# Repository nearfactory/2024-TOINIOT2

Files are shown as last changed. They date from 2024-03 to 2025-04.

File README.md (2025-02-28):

# TOINIOT2 2024 Main-Repo

TOINIOT² 2024年度 開発用メインリポジトリ

回路/基板データ・CADデータ・プログラムコード・プレゼンシートなどのデータ共有/保存用

[現時点での設計](https://a360.co/4b5pnYN)

[チーム内Wiki](https://github.com/nearfactory/2024-TOINIOT2/wiki)

## Follow us!

* X (Twitter) | [@toiniot2](https://x.com/toiniot2/)

* Instagram | [toiniot2](https://www.instagram.com/toiniot2/)

* YouTube | [@TOINIOT2](https://www.youtube.com/channel/UCjIjmQF-FIEdHT7s-4lD-6A)

* Team Blog | [TOINIOT² Blog](https://toiniot2-wakayama.github.io/Main/index.html)

## Presentation-Sheet

### 関西ブロック大会 2025.01.14 掲出
TOINIOT2-Kansai-NoName

### リツモリカップ 2025.02.23 掲出
TOINIOT2-Ritsumori

## Rules
* 📂 Discord上の _#GitHub_ チャンネルを活用してアップロード済みデータについての情報交換をしっかり!

* 🗣 コミュニケーションを頻繁にとる!!!!

* 👣 目標は高く、活動は地道に。

* 🧪 実験を実験を面倒くさがらない、小さな実験の積み重ねでロボットは完成する。

* 📚 率先して技術・知識の習得につとめる。

* 🤜 自らの担当に縛られすぎず、他の担当の手伝いもできるとベスト。

* 👥 自分が困っているときは遠慮なくメンバーにヘルプを求め、メンバーが困っているときは躊躇せずヘルプする!!!!

* 💪 **これが最後のRCJ。やり残しがないようにしよう。**

## Members
* NearFactory [@nearfactory](https://x.com/nearfactory/)

  機体設計・回路/基板設計・プログラム・プレゼンシート　担当

* maguronoosushi0807 [@_Rts87](https://x.com/_Rts87)

  回路/基板設計・プログラム　担当
  
* 010

  広報・ブログ・機体組立て　担当

* tobi

  電池監視員　担当

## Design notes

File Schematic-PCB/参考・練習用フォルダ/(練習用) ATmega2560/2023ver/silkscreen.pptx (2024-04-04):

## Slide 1

+

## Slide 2

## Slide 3

LineSensor

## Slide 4

BallSensor

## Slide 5

Camera

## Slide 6

DirSensor

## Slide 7

A

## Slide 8

B

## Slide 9

C

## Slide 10

MD1

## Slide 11

MD2

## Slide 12

PWR

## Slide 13

MainBoard

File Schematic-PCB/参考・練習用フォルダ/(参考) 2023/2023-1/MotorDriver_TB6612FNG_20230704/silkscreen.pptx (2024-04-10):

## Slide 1

+

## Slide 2

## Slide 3

M1

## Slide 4

M2

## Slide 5

M3

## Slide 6

M4

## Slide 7

MD

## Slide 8

PWR

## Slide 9

+5V

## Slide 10

+6.6V

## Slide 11

MotorDriver

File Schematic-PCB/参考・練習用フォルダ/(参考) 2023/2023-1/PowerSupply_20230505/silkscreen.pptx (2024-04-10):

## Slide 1

+

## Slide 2

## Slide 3

Power

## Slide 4

VIN

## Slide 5

MD

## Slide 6

Main

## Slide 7

Line

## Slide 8

Kicker

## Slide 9

DCDC
Conv.

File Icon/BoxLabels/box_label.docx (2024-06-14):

SENSOR

CRIMPING

BATTERY & CHARGER

OMNI WHEEL

CABLE

3D-PRINTERED ITEM

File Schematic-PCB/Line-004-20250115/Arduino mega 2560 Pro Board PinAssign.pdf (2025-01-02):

3.0.1 2025.01.01

D32 | Line-01
D34 | Line-02
D38 | Line-03
D37 | Line-04
D36 | Line-05

General Pin Input/Output

D33 | Line-06
D39 | Line-07
D4 | Line-08
D12 | Line-09
D14 | Line-10
D15 | Line-11
D16 | Line-12
D17 | Line-13
D22 | Line-14
D29 | Line-15
D24 | Line-16
D25 | Line-17
D26 | Line-18
D27 | Line-19
D42 | Line-20
D45 | Line-21
D44 | Line-22
D43 | Line-23
D41 | Line-24
D48 | Line-25
D47 | Line-26
D46 | Line-Front
D5 | Line-Left
D23 | Line-Back
D40 | Line-Right
D13 | LED_BUILTIN
A0 | Line-Left [Raw]
A1 | Line-09 [Raw]
A2 | Line-05 [Raw]
A3 | Line-11 [Raw]
A4 | Line-03 [Raw]
A5 | Line-13 [Raw]
A6 | Line-01 [Raw]
A7 | Line-Back [Raw]
A8 | Line-Front [Raw]
A9 | Line-15 [Raw]
A10 | Line-23 [Raw]
A11 | Line-17 [Raw]
A12 | Line-21 [Raw]
A13 | Line-19 [Raw]
A14 | Line-Right [Raw]
A15 | Line-07 [Raw]

Analog Sensing

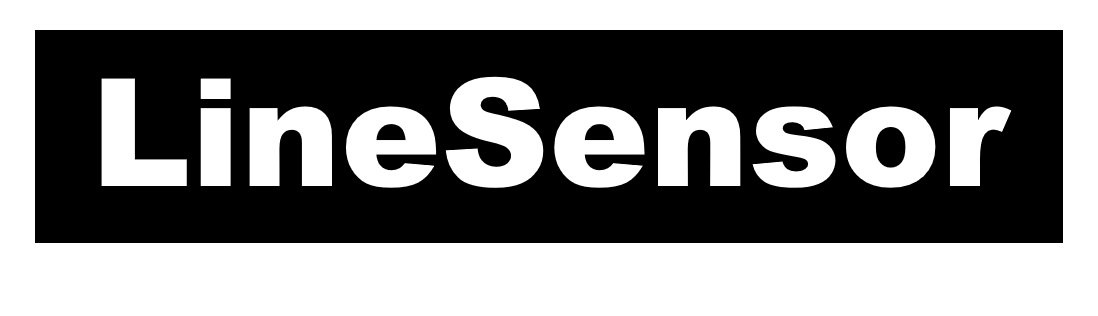
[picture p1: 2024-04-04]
Schematic-PCB/参考・練習用フォルダ/(練習用) ATmega2560/2023ver/LineSensor.png

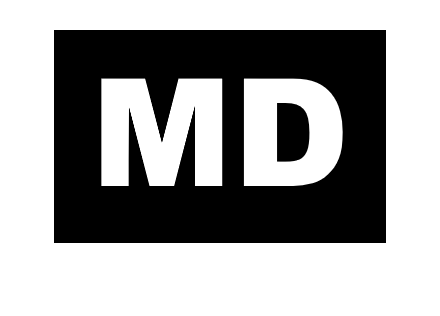
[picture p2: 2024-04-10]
Schematic-PCB/参考・練習用フォルダ/(参考) 2023/2023-1/PowerSupply_20230505/MD.png

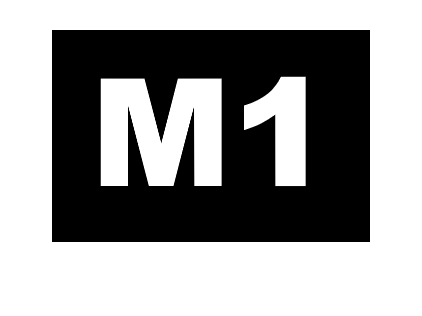
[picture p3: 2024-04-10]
Schematic-PCB/参考・練習用フォルダ/(参考) 2023/2023-1/MotorDriver_TB6612FNG_20230704/M1.png

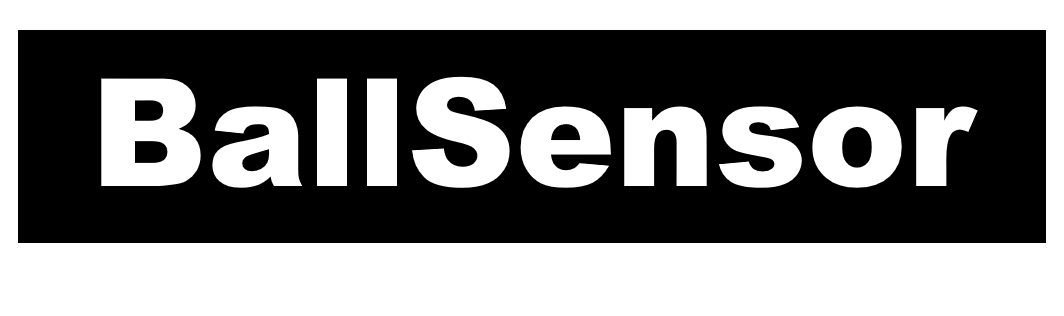
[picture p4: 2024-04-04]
Schematic-PCB/参考・練習用フォルダ/(参考) 2023/2023-1/MainBoard_ATMega2560Pro_20230629/BallSensor.png

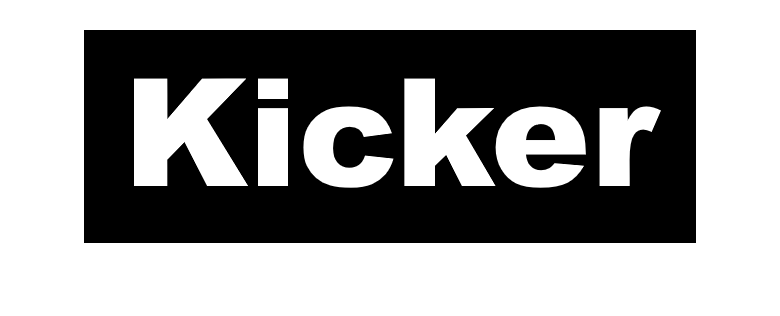
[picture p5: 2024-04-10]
Schematic-PCB/参考・練習用フォルダ/(参考) 2023/2023-1/PowerSupply_20230505/Kicker.png

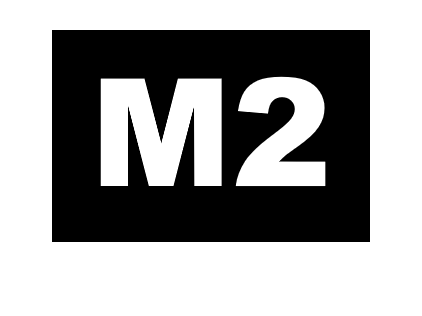
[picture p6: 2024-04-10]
Schematic-PCB/参考・練習用フォルダ/(参考) 2023/2023-1/MotorDriver_TB6612FNG_20230704/M2.png

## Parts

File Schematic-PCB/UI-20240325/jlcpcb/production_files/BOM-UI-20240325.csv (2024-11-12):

Comment | Designator | Footprint | LCSC
0.1uF | C1,C2,C3,C4 | C_0603_1608Metric | C14663
1K | R1,R3,R5,R7,R9 | R_0603_1608Metric | C21190
330 | R10 | R_0603_1608Metric | C23138
10K | R11,R2,R4,R6,R8 | R_0603_1608Metric | C25804

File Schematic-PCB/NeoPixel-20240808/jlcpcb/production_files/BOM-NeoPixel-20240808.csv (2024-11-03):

Comment | Designator | Footprint | LCSC | Quantity
0.1uF | C1,C10,C11,C12,C13,C14,C15,C16,C2,C3,C4,C5,C6,C7,C8,C9 | C_0603_1608Metric | C14663 | 16
WS2812B | D1,D10,D11,D12,D13,D14,D15,D16,D2,D3,D4,D5,D6,D7,D8,D9 | WS2812B 5.0x5.0mm | C2843785 | 16

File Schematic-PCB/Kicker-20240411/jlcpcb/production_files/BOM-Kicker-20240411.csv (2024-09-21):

Comment | Designator | Footprint | LCSC
0.33u | C2,C3 | C_0603_1608Metric | C107058
TSSP58P38 | U1,U2 | Vishay_MINICAST-3Pin | C144844
0.1uF | C5,C7 | C_0603_1608Metric | C14663
330 | R3 | R_0603_1608Metric | C23138
39K | R1,R2 | R_0603_1608Metric | C23153
10K | R4,R5 | R_0603_1608Metric | C25804

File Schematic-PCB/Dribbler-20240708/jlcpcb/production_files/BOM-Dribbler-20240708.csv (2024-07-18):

Comment | Designator | Footprint | LCSC
330 | R1,R2 | R_0603_1608Metric | C23138

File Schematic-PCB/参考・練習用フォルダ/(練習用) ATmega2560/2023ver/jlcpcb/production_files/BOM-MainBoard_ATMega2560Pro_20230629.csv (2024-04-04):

Comment | Designator | Footprint | LCSC
10K | R10,R12,R6,R8 | R_0805_2012Metric | C17414
1K | R11,R13,R5,R7,R9 | R_0805_2012Metric | C17513
330 | R1,R2,R3,R4 | R_0805_2012Metric | C17630
C | C1 | C_0805_2012Metric | C45783

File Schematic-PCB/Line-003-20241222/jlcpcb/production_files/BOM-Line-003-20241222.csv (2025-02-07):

Comment | Designator | Footprint | LCSC | Quantity
100nF | C1,C10,C11,C12,C13,C14,C15,C16,C17,C18,C19,C2,C3,C4,C5,C6,C7,C8,C9 | C_0603_1608Metric | C14663 | 19
10uF | C21,C22 | C_0805_2012Metric | C15850 | 2
1K | R81,R84 | R_0603_1608Metric | C21190 | 2
100 | R86,R87 | R_0603_1608Metric | C22775 | 2
330 | R79,R88 | R_0603_1608Metric | C23138 | 2
Line-PDWN2 | R27,R28,R29,R30 | R_0603_1608Metric | C25804 | 4
RESET | SW1 | Tactile1 | C2844407 | 1
Line-PDWN | R1,R10,R11,R12,R13,R14,R15,R16,R17,R18,R19,R2,R20,R21,R22,R23,R24,R25,R26,R3,R4,R5,R6,R7,R8,R9 | R_0603_1608Metric | C4184 | 26
75 | R31,R32,R33,R34,R35,R36,R37,R38,R39,R40,R41,R42,R43,R44,R45,R46,R47,R48,R49,R50,R51,R52,R53,R54,R55,R56,R57,R58,R59,R60,R61,R62,R63,R64,R65,R66,R67,R68,R69,R70,R71,R72,R73,R74,R75,R76 | R_0603_1608Metric | C4275 | 46
LM393 | U47,U48,U49,U50,U51,U52,U53,U54,U55,U56,U57,U58,U59,U60,U61 | SOP-8_3.9x4.9mm_P1.27mm | C7955 | 15

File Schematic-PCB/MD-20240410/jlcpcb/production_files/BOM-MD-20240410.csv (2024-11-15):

Comment | Designator | Footprint | LCSC | Quantity
0.1u | C7,C8 | C_0603_1608Metric | C14663 | 2
~ | U1,U2,U3,U4 | HTSSOP-16-1EP_4.4x5mm_P0.65mm_EP3.4x5mm | C1855818 | 4
4.7u | C3,C4 | C_0603_1608Metric | C19666 | 2
220n | C10,C12,C14,C2 | C_0603_1608Metric | C21120 | 4
22n | C1,C11,C13,C9 | C_0603_1608Metric | C21122 | 4
2.49k | R12,R16,R4,R8 | R_0603_1608Metric | C22908 | 4
330 | R1 | R_0603_1608Metric | C23138 | 1
10k | R13,R17,R20,R21,R22,R23,R3,R9 | R_0603_1608Metric | C25804 | 8
Conn_main | J8 | TE_1-84953-5_1x15-1MP_P1.0mm_Horizontal | C2914102 | 1
20k | R11,R15,R19,R7 | R_0603_1608Metric | C4184 | 4

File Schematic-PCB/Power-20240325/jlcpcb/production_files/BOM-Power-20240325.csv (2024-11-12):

Comment | Designator | Footprint | LCSC
1K | R4 | R_0603_1608Metric | C21190
1.2K | R3,R7 | R_0603_1608Metric | C22765
1.5K | R1 | R_0603_1608Metric | C22843
10 | R5 | R_0603_1608Metric | C22859
330 | R6 | R_0603_1608Metric | C23138
680 | R2 | R_0603_1608Metric | C23228
22uF | C1,C3 | C_0603_1608Metric | C45783
10uF | C2,C6 | C_0603_1608Metric | C96446
Conn_01x02_Pin | J6 | JST_XH_S2B-XH-A-1_1x02_P2.50mm_Horizontal

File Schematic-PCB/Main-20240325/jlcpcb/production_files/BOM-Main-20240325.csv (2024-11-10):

Comment | Designator | Footprint | LCSC | Quantity
TSSP4038 | U10,U11,U12,U13,U14,U15,U16,U17,U18,U3,U4,U5,U6,U7,U8,U9 | TSSP4038 | C143753 | 16
0.1uF | C10,C11,C12,C3,C4,C5,C6,C7,C8,C9 | C_0603_1608Metric | C14663 | 10
1K | R3,R4 | R_0603_1608Metric | C21190 | 2
330 | R5,R7 | R_0603_1608Metric | C23138 | 2
39K | R10,R11,R12,R13,R14,R15,R18,R19,R20,R21,R22,R23,R24,R25,R8,R9 | R_0603_1608Metric | C23153 | 16
10K | R16,R17,R6 | R_0603_1608Metric | C25804 | 3
0.33uF | C13,C14,C15,C16,C17,C18,C19,C20,C21,C22,C23,C24,C25,C26,C27,C28 | C_0603_1608Metric | C282682 | 16
Conn_MD | J5 | 1.0K-FX-15PWB | C2914102 | 1

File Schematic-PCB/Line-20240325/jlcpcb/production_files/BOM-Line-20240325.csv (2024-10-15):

Comment | Designator | Footprint | LCSC
0.1uF | C2,C3,C4 | C_0603_1608Metric | C14663
1K | R97 | R_0603_1608Metric | C21190
Line-Pulldown | R47,R48,R49,R50,R51,R52,R53,R54,R55,R56,R57,R58,R59,R60,R61,R62,R63,R64,R65,R66,R67,R68,R69,R70,R71,R72,R73,R74,R75,R76,R77,R78,R79,R80,R81,R82,R83,R84,R85,R86,R87,R88,R89,R90,R91,R92 | R_0603_1608Metric | C22809
330 | R93,R94,R95,R96 | R_0603_1608Metric | C23138
75 | R1,R10,R11,R12,R13,R14,R15,R16,R17,R18,R19,R2,R20,R21,R22,R23,R24,R25,R26,R27,R28,R29,R3,R30,R31,R32,R33,R34,R35,R36,R37,R38,R39,R4,R40,R41,R42,R43,R44,R45,R46,R5,R6,R7,R8,R9 | R_0603_1608Metric | C4275
10uF | C5 | C_0603_1608Metric | C96446

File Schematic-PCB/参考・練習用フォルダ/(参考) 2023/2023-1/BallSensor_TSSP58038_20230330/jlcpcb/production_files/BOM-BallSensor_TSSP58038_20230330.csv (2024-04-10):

Comment | Designator | Footprint | LCSC
TSSP58038 | U1,U10,U11,U12,U13,U14,U15,U16,U2,U3,U4,U5,U6,U7,U8,U9 | TSSP58038 | C144844
C | C18,C19,C20,C21,C22,C23,C24,C25 | C_0603_1608Metric | C14663
C | C10,C11,C12,C13,C14,C15,C16,C17,C2,C3,C4,C5,C6,C7,C8,C9 | C_0603_1608Metric | C1615
~ | D10,D11,D12,D13,D14,D15,D16,D17,D2,D3,D4,D5,D6,D7,D8,D9 | WS2812B | C2761795
R | R1,R10,R11,R12,R13,R14,R15,R16,R17,R2,R3,R4,R5,R6,R7,R8,R9 | R_0603_1608Metric | C4275
Conn_01x20_Male | J1 | IDC-Header_2x10_P2.54mm_Vertical

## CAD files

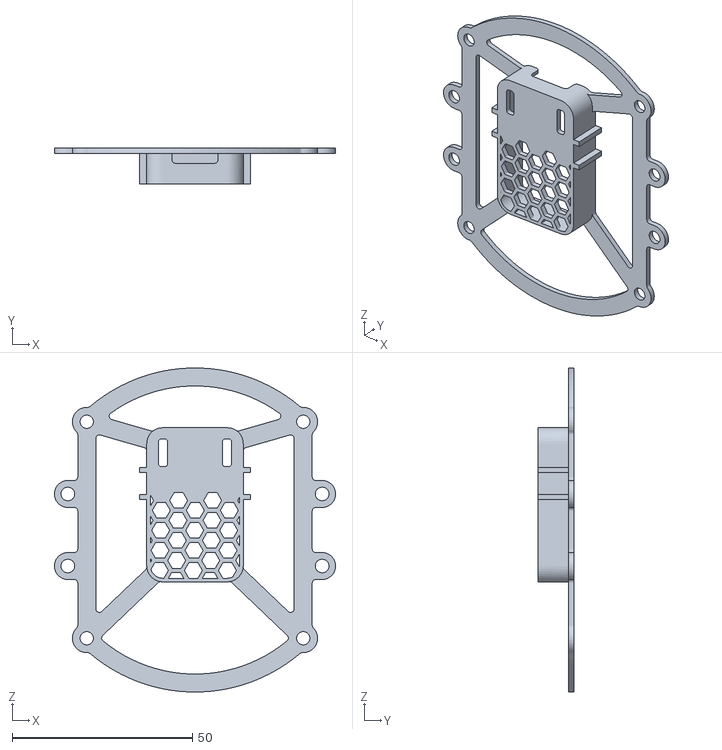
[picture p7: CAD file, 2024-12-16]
Design/3D [自家製]/camera-supporter/[iot2][006][camera-supporter][main].stl
78.1 x 10.0 x 90.0

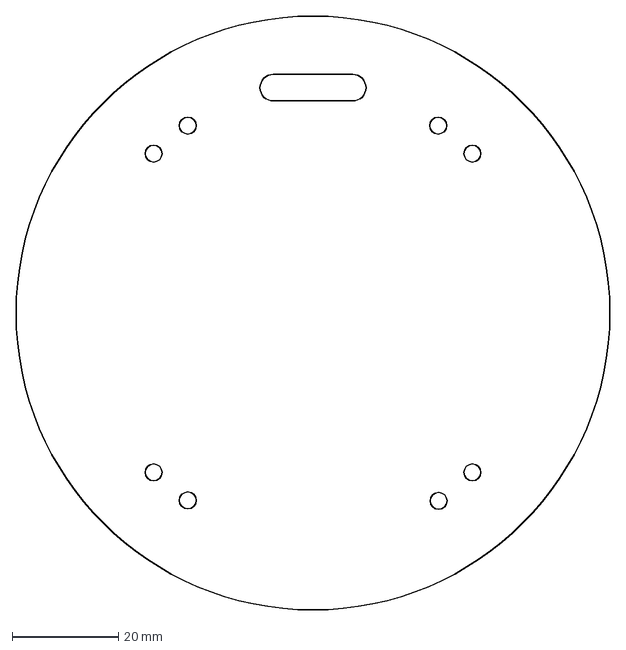
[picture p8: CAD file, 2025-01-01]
Schematic-PCB/Main-003-20241229/outline/[iot2][003][main-003-outline].dxf
112.0 x 112.0 mm

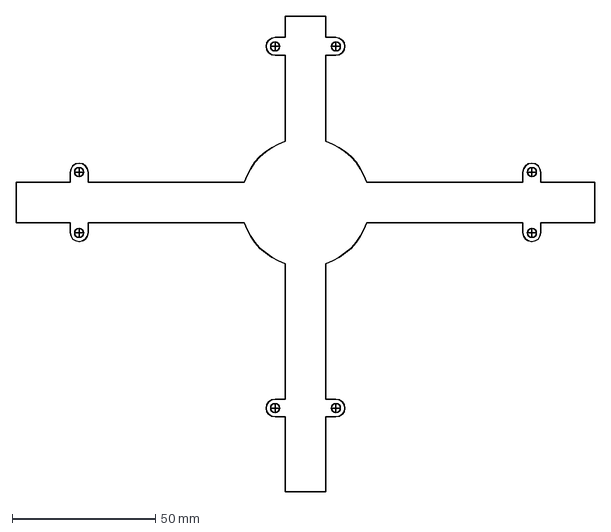
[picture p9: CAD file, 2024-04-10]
Schematic-PCB/参考・練習用フォルダ/(参考) 2023/2023-1/LineSensor_20230418/main.dxf
202.0 x 166.0 mm

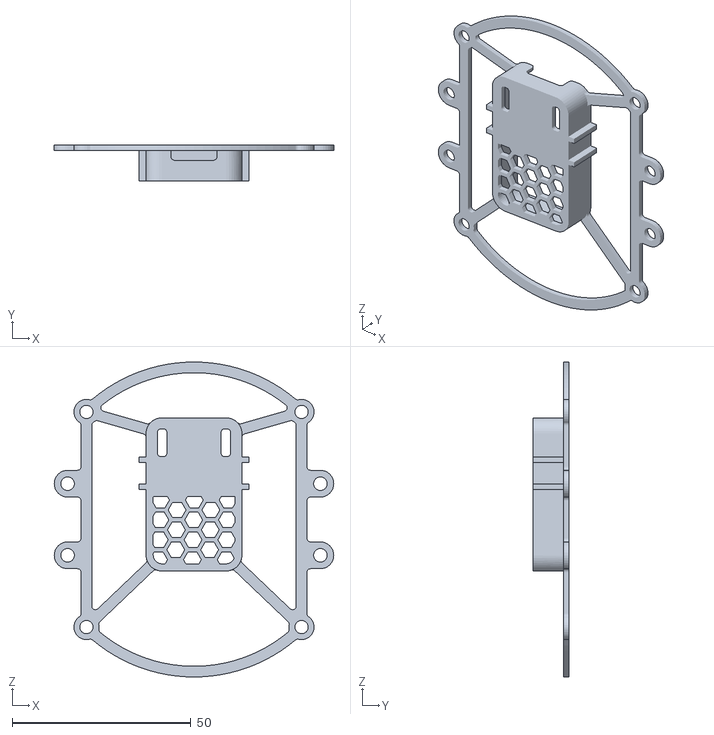
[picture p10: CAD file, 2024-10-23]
Design/3D [自家製]/camera-supporter/[iot2][005][camera-supporter][main].stl
78.1 x 10.0 x 88.0

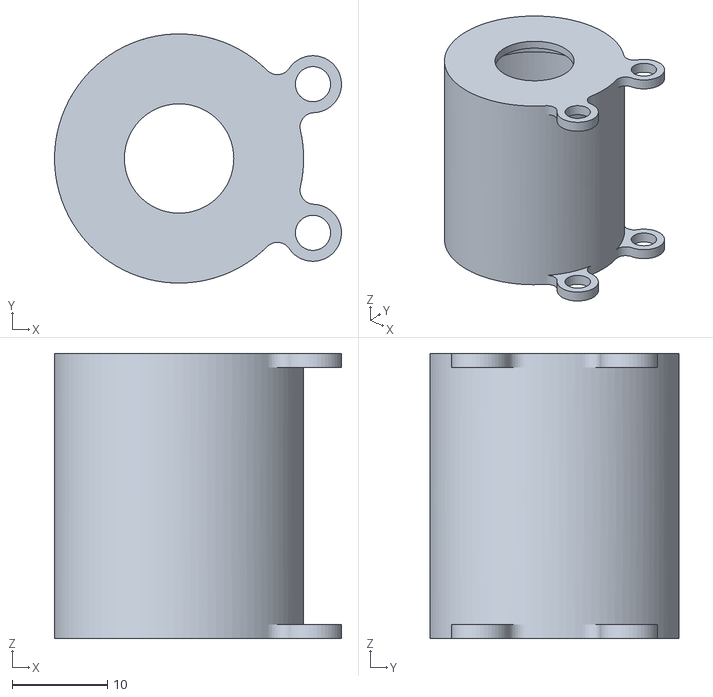
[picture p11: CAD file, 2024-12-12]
Design/3D [自家製]/dribbler/dribbler-004/[iot2][003][dribbler-004][main].stl
30.2 x 26.2 x 30.0

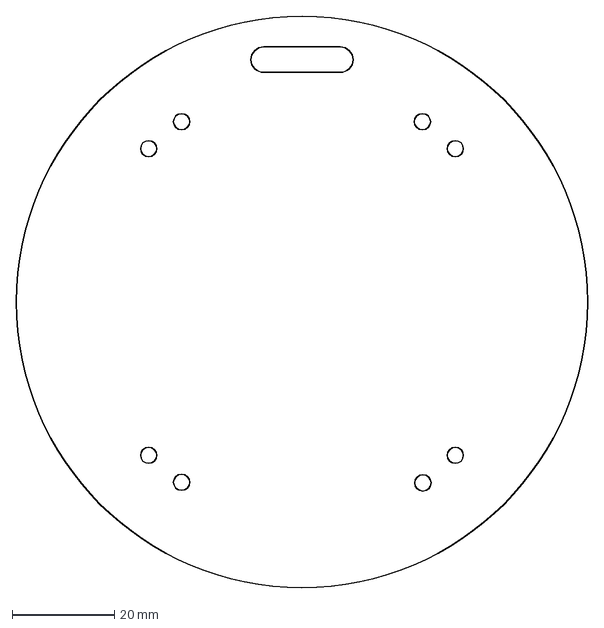
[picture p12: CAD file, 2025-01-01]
Schematic-PCB/Main-003-20241229/outline/[iot2][002][main-003-outline].dxf
112.0 x 112.0 mm

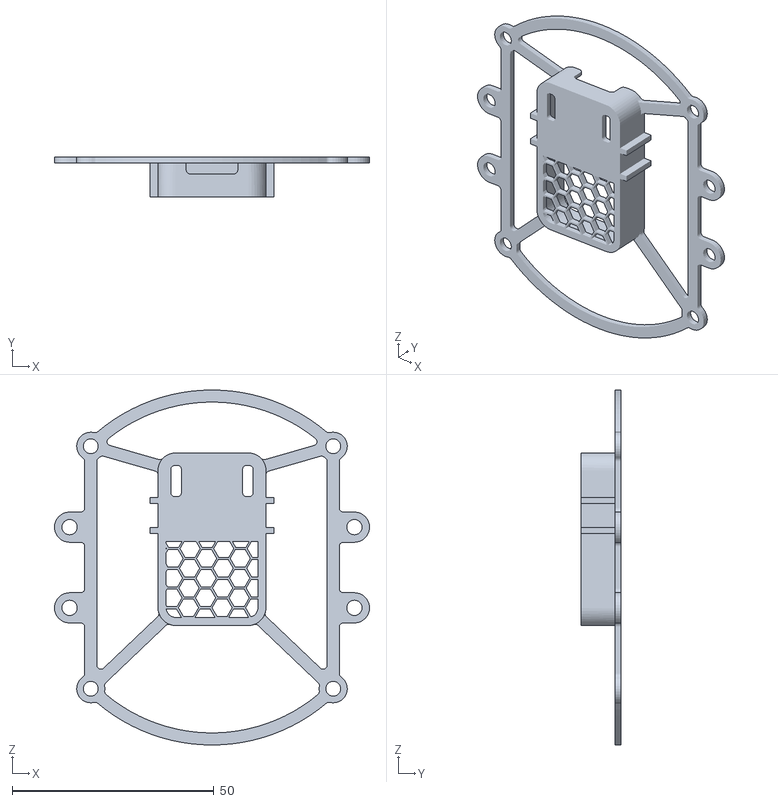
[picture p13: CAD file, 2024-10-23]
Design/3D [自家製]/camera-supporter/[iot2][004][camera-supporter][main].stl
78.1 x 10.0 x 88.0

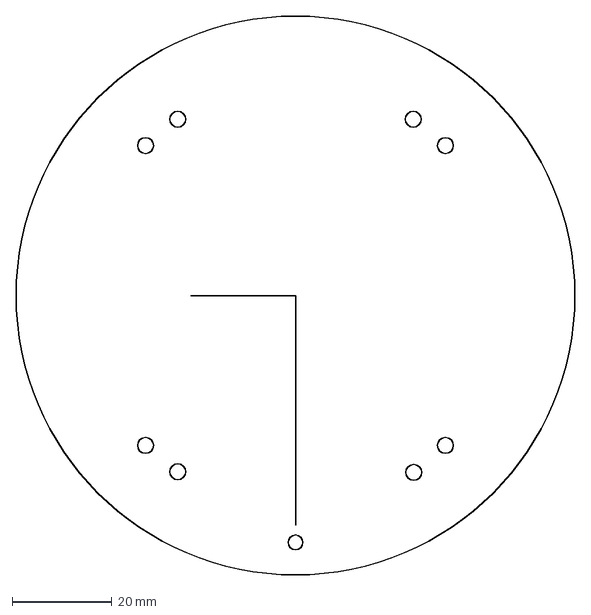
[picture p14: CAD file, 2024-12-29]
Schematic-PCB/Main-003-20241229/outline/[iot2][001][main-003-outline].dxf
112.0 x 112.0 mm

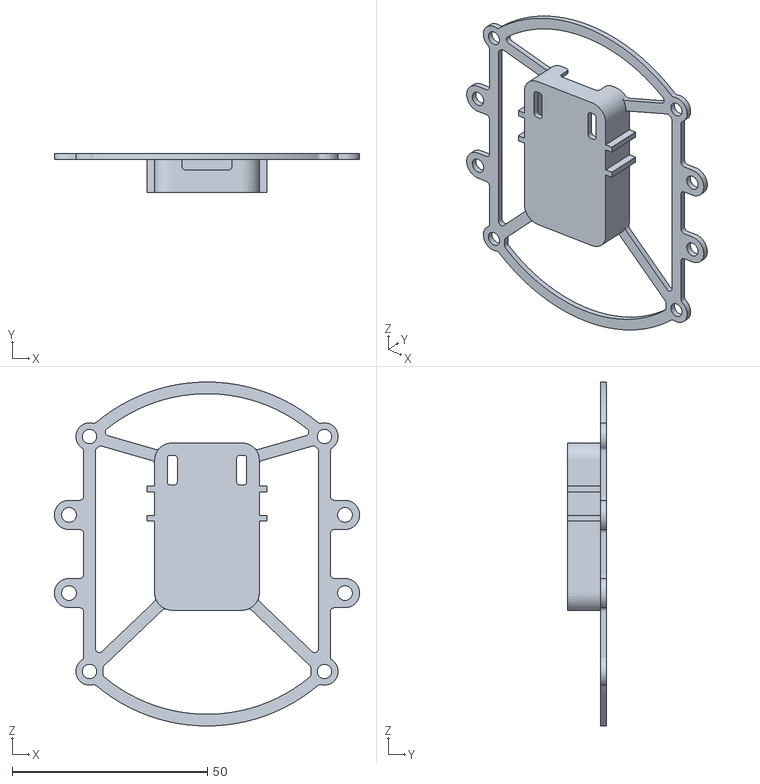
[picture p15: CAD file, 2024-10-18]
Design/3D [自家製]/camera-supporter/[iot2][003][camera-supporter][main].stl
78.1 x 10.0 x 88.0

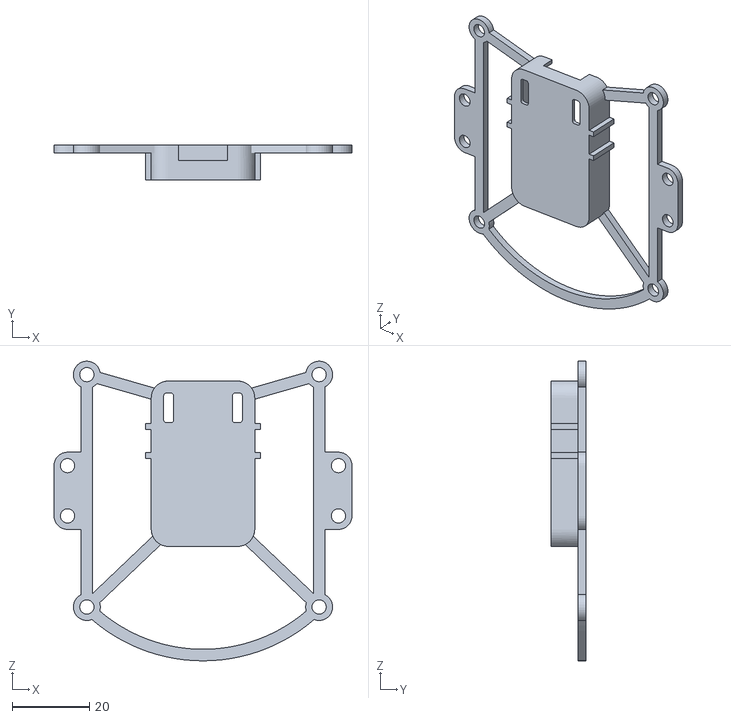
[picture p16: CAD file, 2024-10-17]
Design/3D [自家製]/camera-supporter/[iot2][002][camera-supporter][main].stl
77.1 x 9.00 x 77.5

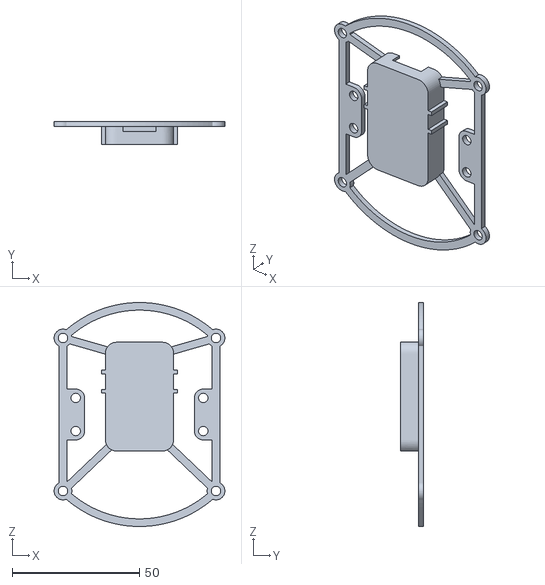
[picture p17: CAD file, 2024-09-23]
Design/3D [自家製]/camera-supporter/[iot2][001][camera-supporter][main].stl
67.1 x 9.00 x 88.0

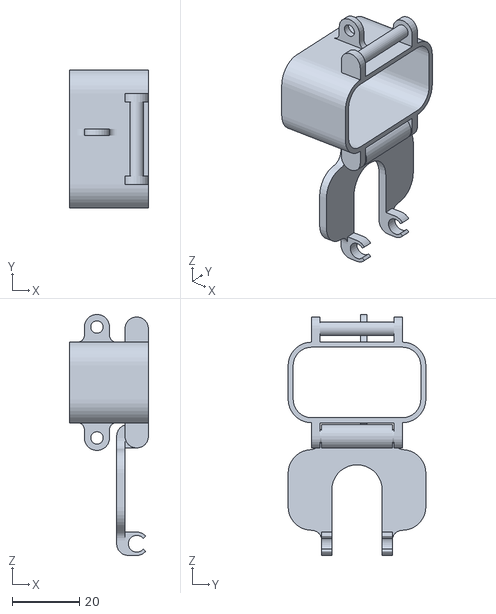
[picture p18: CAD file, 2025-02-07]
Design/3D [1000万]/[iot2][battery-R-lid][001].stl
23.5 x 41.0 x 71.7

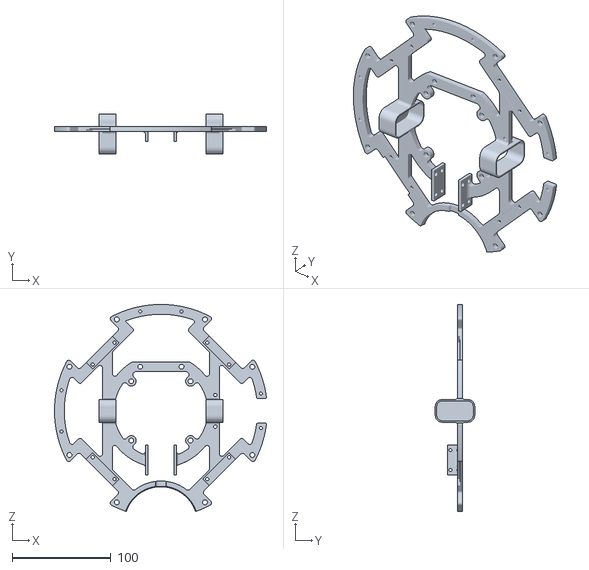
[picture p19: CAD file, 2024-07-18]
Design/3D [外注決定]/002-01/002-Top-004.stl
215.1 x 40.2 x 210.1

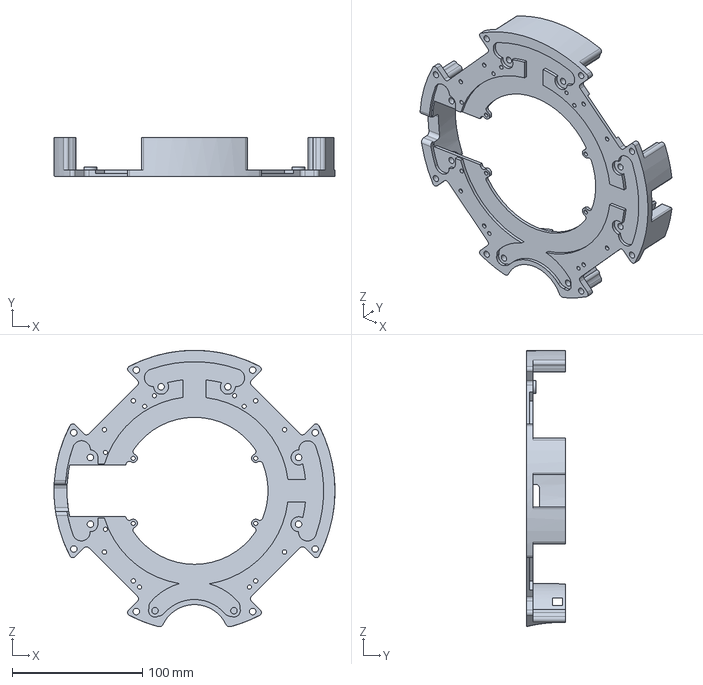
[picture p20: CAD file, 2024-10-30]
Design/3D [外注決定]/002-02/002-bottom-02.step
216.0 x 30.0 x 212.4 mm

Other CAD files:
Design/3D [外注決定]/003-01/iot2 003 top 3.stl
Design/3D [自家製]/actuator-cover/motorcover#002[iot2].stl
Design/3D [自家製]/ball-cover-for-main003/[iot2][ball-cover-m3][002].stl
Design/3D [自家製]/battery/[iot2][003][battery-2-2].stl
Design/3D [外注決定]/002-01/002-Bottom-002.stl
Design/3D [外注決定]/002-01/002-Bottom-004.stl
Design/3D [外注決定]/002-01/002-Bottom.stl
Design/3D [外注決定]/002-01/002-Top-002.stl
Design/3D [外注決定]/002-01/002-Top-003.stl
Design/3D [外注決定]/002-01/002-Top.stl
Design/3D [外注決定]/002-02/002-top-02.step
Design/3D [外注決定]/002-02/[iot2][002][bottom][2].stl
Design/3D [外注決定]/002-02/[iot2][002][top][2].stl
Design/3D [外注決定]/003-01/iot2 003 bottom 1.stl
Design/3D [外注決定]/003-01/iot2 003 bottom 2.stl
Design/3D [外注決定]/003-01/iot2 003 top 1.stl
Design/3D [外注決定]/003-01/iot2 003 top 2.stl
Design/3D [自家製]/actuator-cover/motorcover#001[iot2].stl
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

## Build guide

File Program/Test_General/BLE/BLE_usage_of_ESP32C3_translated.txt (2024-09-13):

こんにちは。
ここで、BLE を使用して 2 つの ESP32C3 を接続する方法の例を確認できます。
https://wiki.seeedstudio.com/
XIAO_ESP32C3_Bluetooth_使用法/
よろしく！
EICO
テクニカルサポートチームを参照

こんにちは。
私はサイエンスクラブに所属する日本人学生です。
私は部活動として、人間が制御せずにサッカーをするロボットを作っています。
無線通信を行うために、ESP32C3モジュールを使用する予定です。
しかし、2台のESP32C3を無線で接続する方法が見つからなかったので、それが可能かどうかを確認したいと思います。
ESP32C3を2つ接続する方法を教えていただければ幸いです。
ありがとう。

ご回答ありがとうございます。
ある ESP32C3 を別の ESP32C3 に Bluetooth 経由で接続できるかどうかを確認したいと思います。
回答のリンクには、2 台の ESP32C3 を Bluetooth 経由で接続する例はなく、1 台の ESP32C3 を Bluetooth 経由でスマートフォンまたは PC に接続するだけです。
2台のESP32C3を接続する方法を教えていただけますか?
ありがとう：）

こんにちは。
なるほど、S3 の例を参照してください。C3 でも機能するはずです。
https://wiki.seeedstudio.com/
xiao_esp32s3_bluetooth/
よろしく！

ESP32C3を別のESP32C3に接続できるか確認したい
Bluetooth経由のESP32C3。
あなたの応答のリンクには、2 つの ESP32C3 を接続する例がありません。
Bluetooth 経由ですが、1 つの ESP32C3 をスマートフォンまたは PC に接続するだけです。
ブルートゥース。
2台のESP32C3を接続する方法を教えていただけますか?
ありがとう：）

こんにちは。
ここで、BLE を使用して 2 つの ESP32C3 を接続する方法の例を確認できます。
https://wiki.seeedstudio.com/
XIAO_ESP32C3_Bluetooth_使用法/
よろしく！

こんにちは。
ご返答ありがとうございます。
ESP32S3の技術資料を参考にさせていただきます。
ご協力ありがとうございました！

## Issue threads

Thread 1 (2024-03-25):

モーター選定

Toiniot2-Wakayama, 2024-03-25:
- Pololu
- Maxon
- 秋月モーター
- 中華コアレス
- その他

選定時は回転数 (RPM) とトルク (mNm、kg*cmなど）に着目の上で選定する

nearfactory, 2024-03-28:
当初予定していたmaxonモーターと異なるモーターを選定したい

4.5W・13100rpm・29.9 mNm
1-4コ：23,800
5-19コ：21,000

nearfactory, 2024-03-28:
新モーター
https://www.maxongroup.co.jp/maxon/view/product/motor/dcmotor/re/re16/118714
https://www.maxongroup.co.jp/maxon/view/product/motor/dcmotor/re/re16/118715

2つの違い：定格電圧が9Vか12Vか

nearfactory, 2024-04-13:
一旦pololuもmaxonでも対応できるモーターブラケットの設計を完了済み
→maxonが入手できるまではpololu 25D 9.7:1で行く、手に入り次第maxonでやってみる

Closed 2024-06-14.

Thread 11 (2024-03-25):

電源基板回路設計

Toiniot2-Wakayama, 2024-03-25:

nearfactory, 2024-03-28:
電圧監視回路、ヒューズ、電圧計、DCDCコンバーターを搭載予定

DCDCコンバーターについては、従来のOKL-T/6-W12Cを使用するか、新しいDCDCコンバーターを探すか
→ 効率、安全性、価格、性能等を鑑みて検討するべし

nearfactory, 2024-03-29:
DCDCコンバーターは従来のモノを使う予定
→電源基板自体を物理的に保護するようなカバーが欲しいところではある
（偶発的な接触、ショートからの保護等の問題解決、ナット等が落ちて入りこむことを防ぐ目的）

Closed 2024-06-14.

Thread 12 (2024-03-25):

電池選定

Toiniot2-Wakayama, 2024-03-25:
- Li-Fe 2セル
- Li-Fe 3セル
- Ni-MH 8.4V
- Ni-MH 9.6V
- その他充電池

電池容量、電圧、安全性、価格等に着目の上選定する

nearfactory, 2024-03-29:
現状では
・Li-Fe 3セル 9.9V 1450mAh
が有力候補ではある
ただいつもの
・Ni-MH 9.6V 1600mAh
も決して悪くはない、サイズ感的にちょっとあれやけど

nearfactory, 2024-03-29:
**Li-Fe3セル 9.9V 1450mAh**
https://kondo-robot.com/product/life_f3_1450
**↑専用充電器**
https://kondo-robot.com/product/bx-20lf

nearfactory, 2024-03-29:
**Ni-MH 9.6V 1600mAh**
https://www.amazon.co.jp/Melasta-%E3%83%8B%E3%83%83%E3%82%B1%E3%83%AB%E6%B0%B4%E7%B4%A0%E3%83%90%E3%83%83%E3%83%86%E3%83%AA%E3%83%BC-%E3%83%9F%E3%83%8B%E3%82%B3%E3%8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
**↑専用充電器**
https://www.amazon.co.jp/Melasta-%E3%83%8B%E3%83%83%E3%82%B1%E3%83%AB%E6%B0%B4%E7%B4%A0%E3%83%90%E3%83%83%E3%83%86%E3%83%AA%E3%83%BC%E5%85%85%E9%9B%BB%E5%99%A8-%E6%A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

nearfactory, 2024-04-13:
設計はLi-Fe 3セル 9.9V 1450mAhで行っている
Ni-MHへの対応も考えてもいいが、キッカーの搭載が厳しくなる恐れがある（縦にして入れれば何とかなるが...）

Closed 2024-06-14.

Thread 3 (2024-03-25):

カメラ選定

Toiniot2-Wakayama, 2024-03-25:
- 処理速度
- 画素数
- 画質
- プログラミング言語
- サイズ
- 焦点距離

等に着目の上選定する

nearfactory, 2024-03-28:
今のところ
UnitVかPixy2.1を使用予定

UnitV
低価格・低処理速度・普通解像度・Micropython・UART/SPIでの通信

Pixy
高価格・普通処理速度・普通解像度・プログラムなし・I2C/UART/SPIでの通信

使い慣れたPixyで行くか、UnitVという新しい道を切り開くか。

maguronoosushi0807, 2024-03-29:
処理速度の問題を解決できるなら安価なUnitVを使用してみるのでいいと思います。

軽く調べた感じ、デフォルトの重いファームウェアから必要な部分だけを抽出して軽量化しているようです。
https://blog.shirokuma89.dev/20240328/ 「カメラ」の段落より

Closed 2024-06-14.

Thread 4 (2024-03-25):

マイコン選定

Toiniot2-Wakayama, 2024-03-25:
**マイコンは2つ以上使用予定のため、それぞれに適応したマイコンを選定すること**

- メイン処理用
- ボールセンサ用
- ラインセンサ用
- （距離センサ用）
- （MD用）
- （UI用）

等があるため、それぞれに合ったマイコンを選定すること（チップのモノがあるかJLCPCBにどうかも要チェック）

nearfactory, 2024-03-28:
teensy4.1
高処理速度・高価格・SMD化ほぼ不可能・普通サイズ・普通ピン数

STM32
高処理速度・価格？・SMD対応・SMDの場合小サイズ・普通ピン数

STM32については機体に搭載する場合はSMD化が必須→ボードが特大サイズのため

nearfactory, 2024-03-29:
Teesy4.1を使う場合、拡張基板を自作したうえで使用する必要がある
→開発基板に表面実装でしか使えないピンがある
→それを使えるようにするために拡張基板を作る必要がある

nearfactory, 2024-03-29:
teensy4.1は動作電圧が3.3V、
STM32も動作電圧は3.6Vぐらい

nearfactory, 2024-04-13:
メインマイコンにはteensy4.1、サブマイコン（無線・UIなど）でESP32C3（seeed）を使用
ラインセンサ専用マイコンでATmega2560（チップ）を使用予定
→ATmega2560の回路については山本さんor他の誰かしらに必ずDRを求めること（特に書き込み用シリアル変換周り）

Closed 2024-06-14.

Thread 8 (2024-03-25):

ボールセンサ基板回路設計

Toiniot2-Wakayama, 2024-03-25:

nearfactory, 2024-03-29:
使用するセンサ素子で悩み中

TSSP58038かTSSP4038で悩んでる
TSSP58038→2023で使ったやつ、特性もある程度把握できている
TSSP4038→2023でedgeが使ってた、距離と角度に応じたセンサ値の変動が58038よりもきれい、ただ使ったことがない

nearfactory, 2024-03-29:
**TSSP58038**
https://www.mouser.jp/ProductDetail/Vishay-Semiconductors/TSSP58038?qs=lgjwDzixuo29LR1eAo9EoA%3D%3D

**TSSP4038**
https://www.mouser.jp/ProductDetail/Vishay-Semiconductors/TSSP4038?qs=lgjwDzixuo3Ja5hn%252BEmOdw%3D%3D

nearfactory, 2024-03-29:
ちなみにセンサ素子自体の形も微妙に違う
58038は受光部が1/4球+半円柱なのに対して、4038は完全に受光部が半球になってる
多分そのせいで受光時の感度が違う

nearfactory, 2024-03-31:
両方買ってみてセンサ素子による値の違いを見てみるのもあり
→プレゼンシートにかけるのでは？（実験・データ）

Closed 2024-06-14.

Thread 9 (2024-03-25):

ラインセンサ基板回路設計

Toiniot2-Wakayama, 2024-03-25:

nearfactory, 2024-03-30:
使用するLEDの選定について
コート色である緑の補色の**赤色**LEDを使用したい
半値角は30度のモノがいいのでは
→光漏れが少なくなる→ラインセンサカバーの制作が不要になるのでは

今のところの選定
・無極性3mm赤色LED 625nm OSRRH23133A（https://akizukidenshi.com/catalog/g/g111347/）
・3mm赤色LED 624nm 30度 OS5RKA3131A（https://akizukidenshi.com/catalog/g/g104767/）
・低消費3mm 赤色 LED 625nm 1mA OSR5PA3133A-1MA（https://akizukidenshi.com/catalog/g/g116908/）
のうちのどれか

nearfactory, 2024-03-30:
センサ素子自体は、現状のままだとTHTのいつものNJL7502Lを使う予定
（ https://akizukidenshi.com/catalog/g/g102325/ ）

nearfactory, 2024-03-31:
**LED選定について**
個人的には半値角の違いでどのように見えかたが変わるのかを実験してみるのも全然あり

→プレゼンシートにもかけるかも（実験とデータを示そう）

nearfactory, 2024-04-02:
**LEDの選定について**
半減角の認識が違ったので、選定やり直しです。
2023に使っていたものは半減角が60度だったので、それと同じようなものを赤色LEDで調べていたところ、70度のものが見つかりました。
再度LEDの半減角を調べた上で検討していきたいと思います。

・3mm赤色LED 625nm 70度 OSR5JA3Z74A
https://akizukidenshi.com/catalog/g/g111333/

nearfactory, 2024-04-06:
ラインセンサ専用マイコンを積む予定ですが、今のところはATmega2560を積む予定です。
アナログピンが16本あるので、それを使って自動閾値調整をやりたいです。
今考えているのは、閾値設定モードを予め用意しておき、予めいくつかのセンサをアナログピンにも並列で繋いでおき（基本的にすべてのセンサはデジタルで読む予定）そのアナログ値から閾値を自動で算出。その後、FET（MOSFET）に繋いだピン（PWM）でセンサの電源電圧を変更する、という流れです。

nearfactory, 2024-04-13:
コンパレータ
秋月での購入 or JLCPCBでのAssembly
両方ともめどは立っているが...
回路関連はedgeのブログを参考にしつつ山本さんにDR依頼してもいいかも

Closed 2024-06-14.

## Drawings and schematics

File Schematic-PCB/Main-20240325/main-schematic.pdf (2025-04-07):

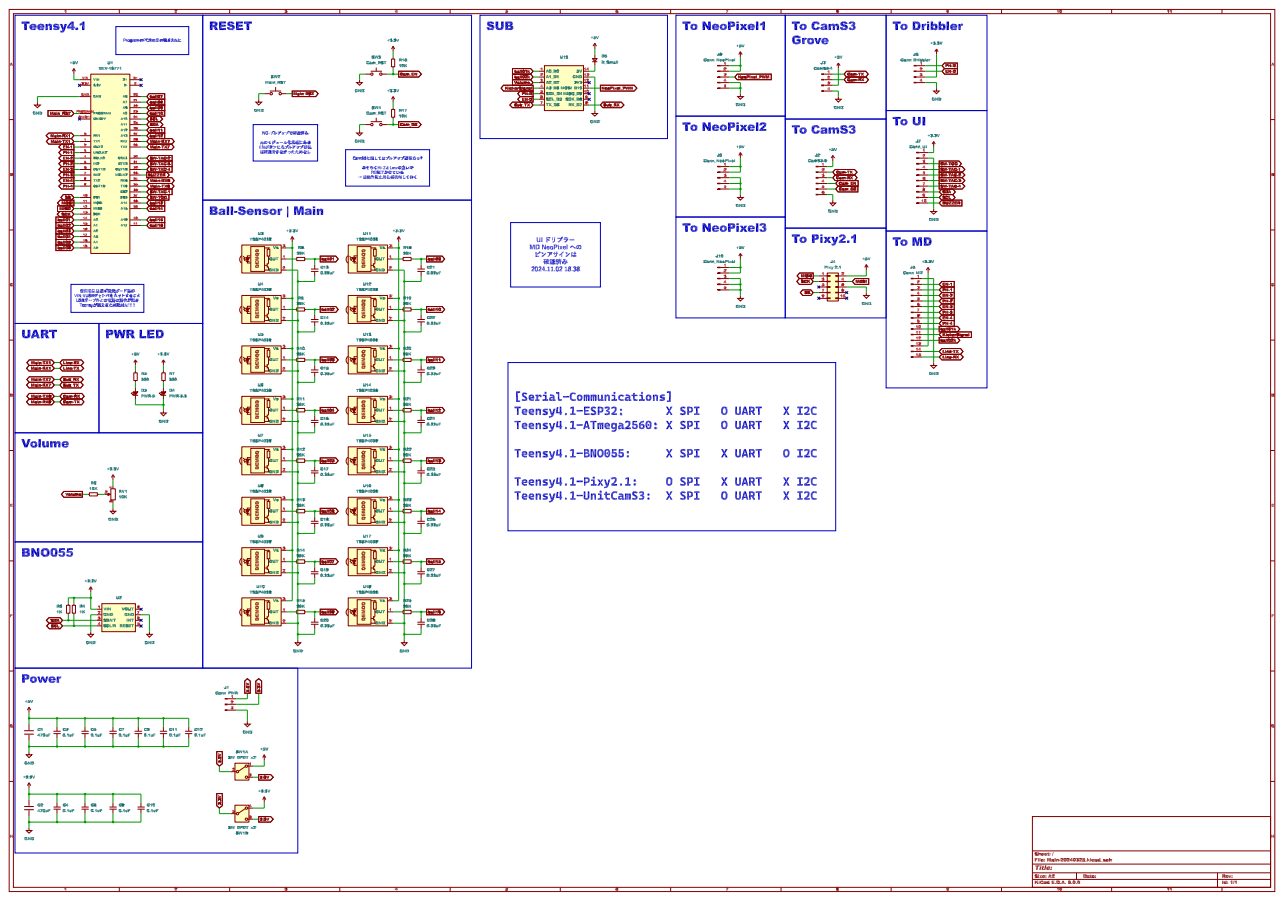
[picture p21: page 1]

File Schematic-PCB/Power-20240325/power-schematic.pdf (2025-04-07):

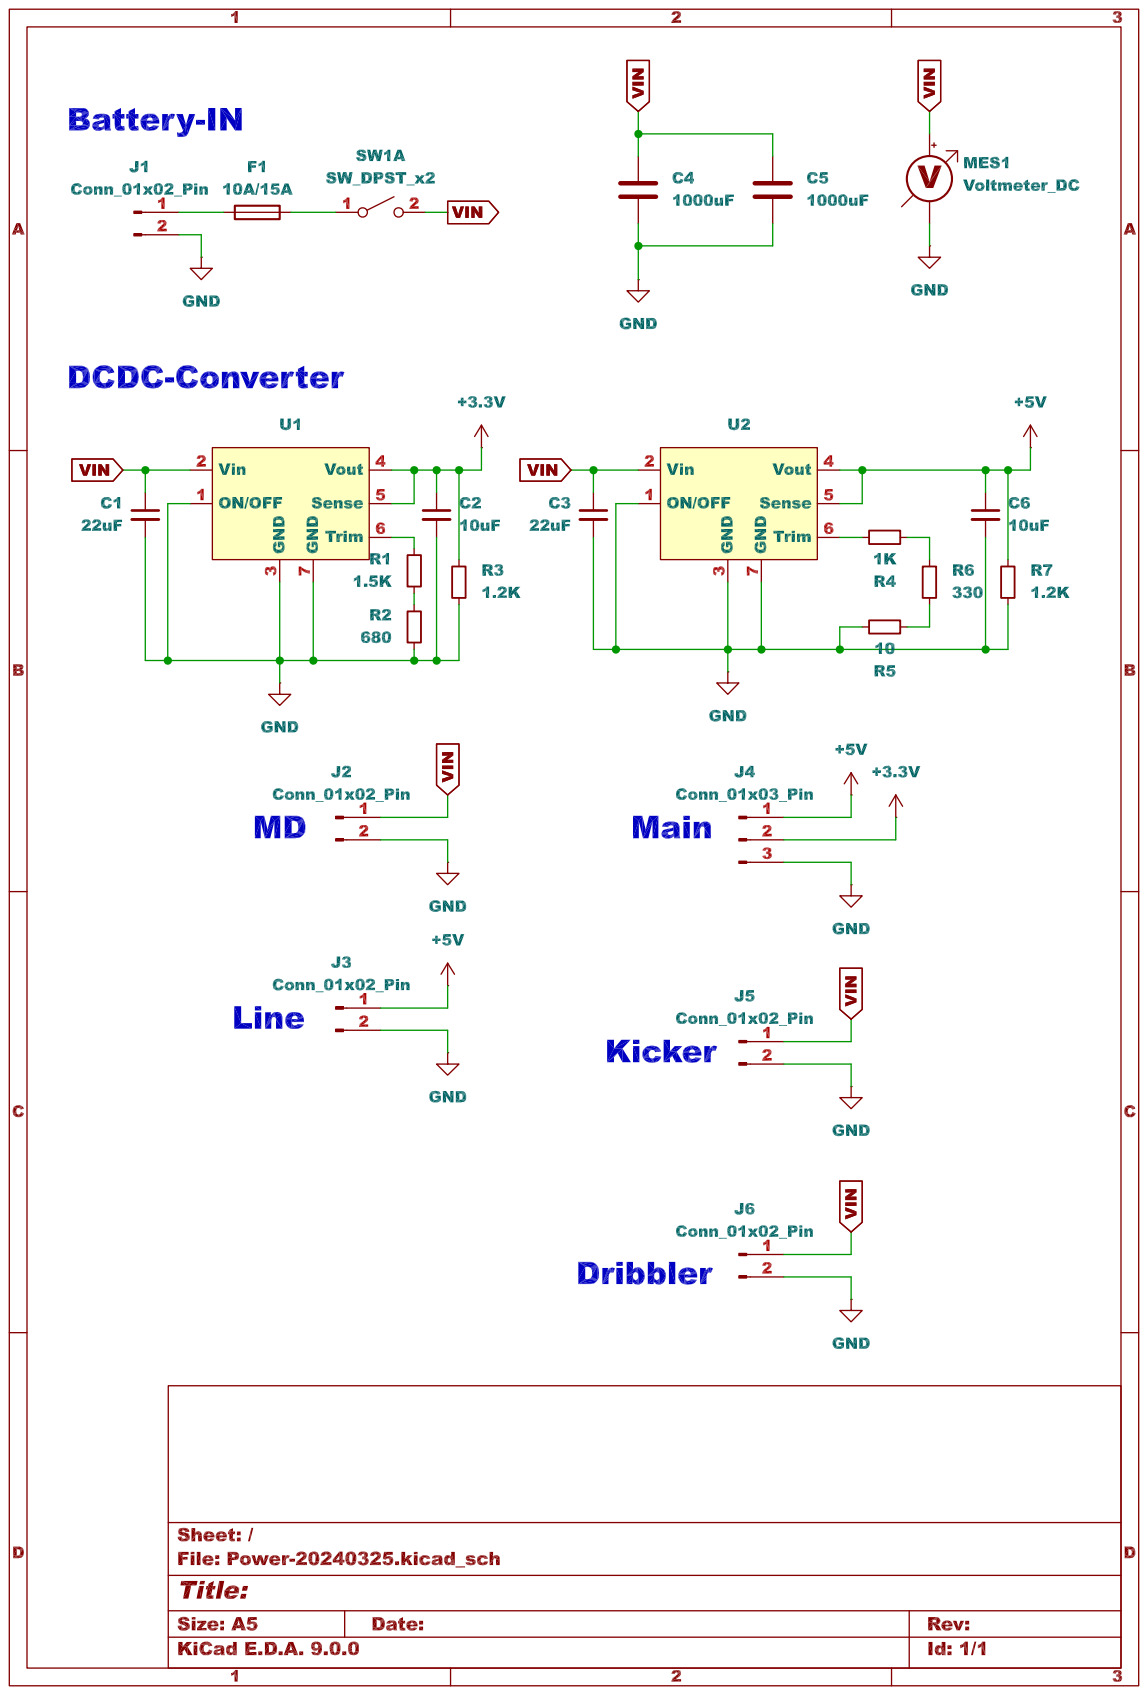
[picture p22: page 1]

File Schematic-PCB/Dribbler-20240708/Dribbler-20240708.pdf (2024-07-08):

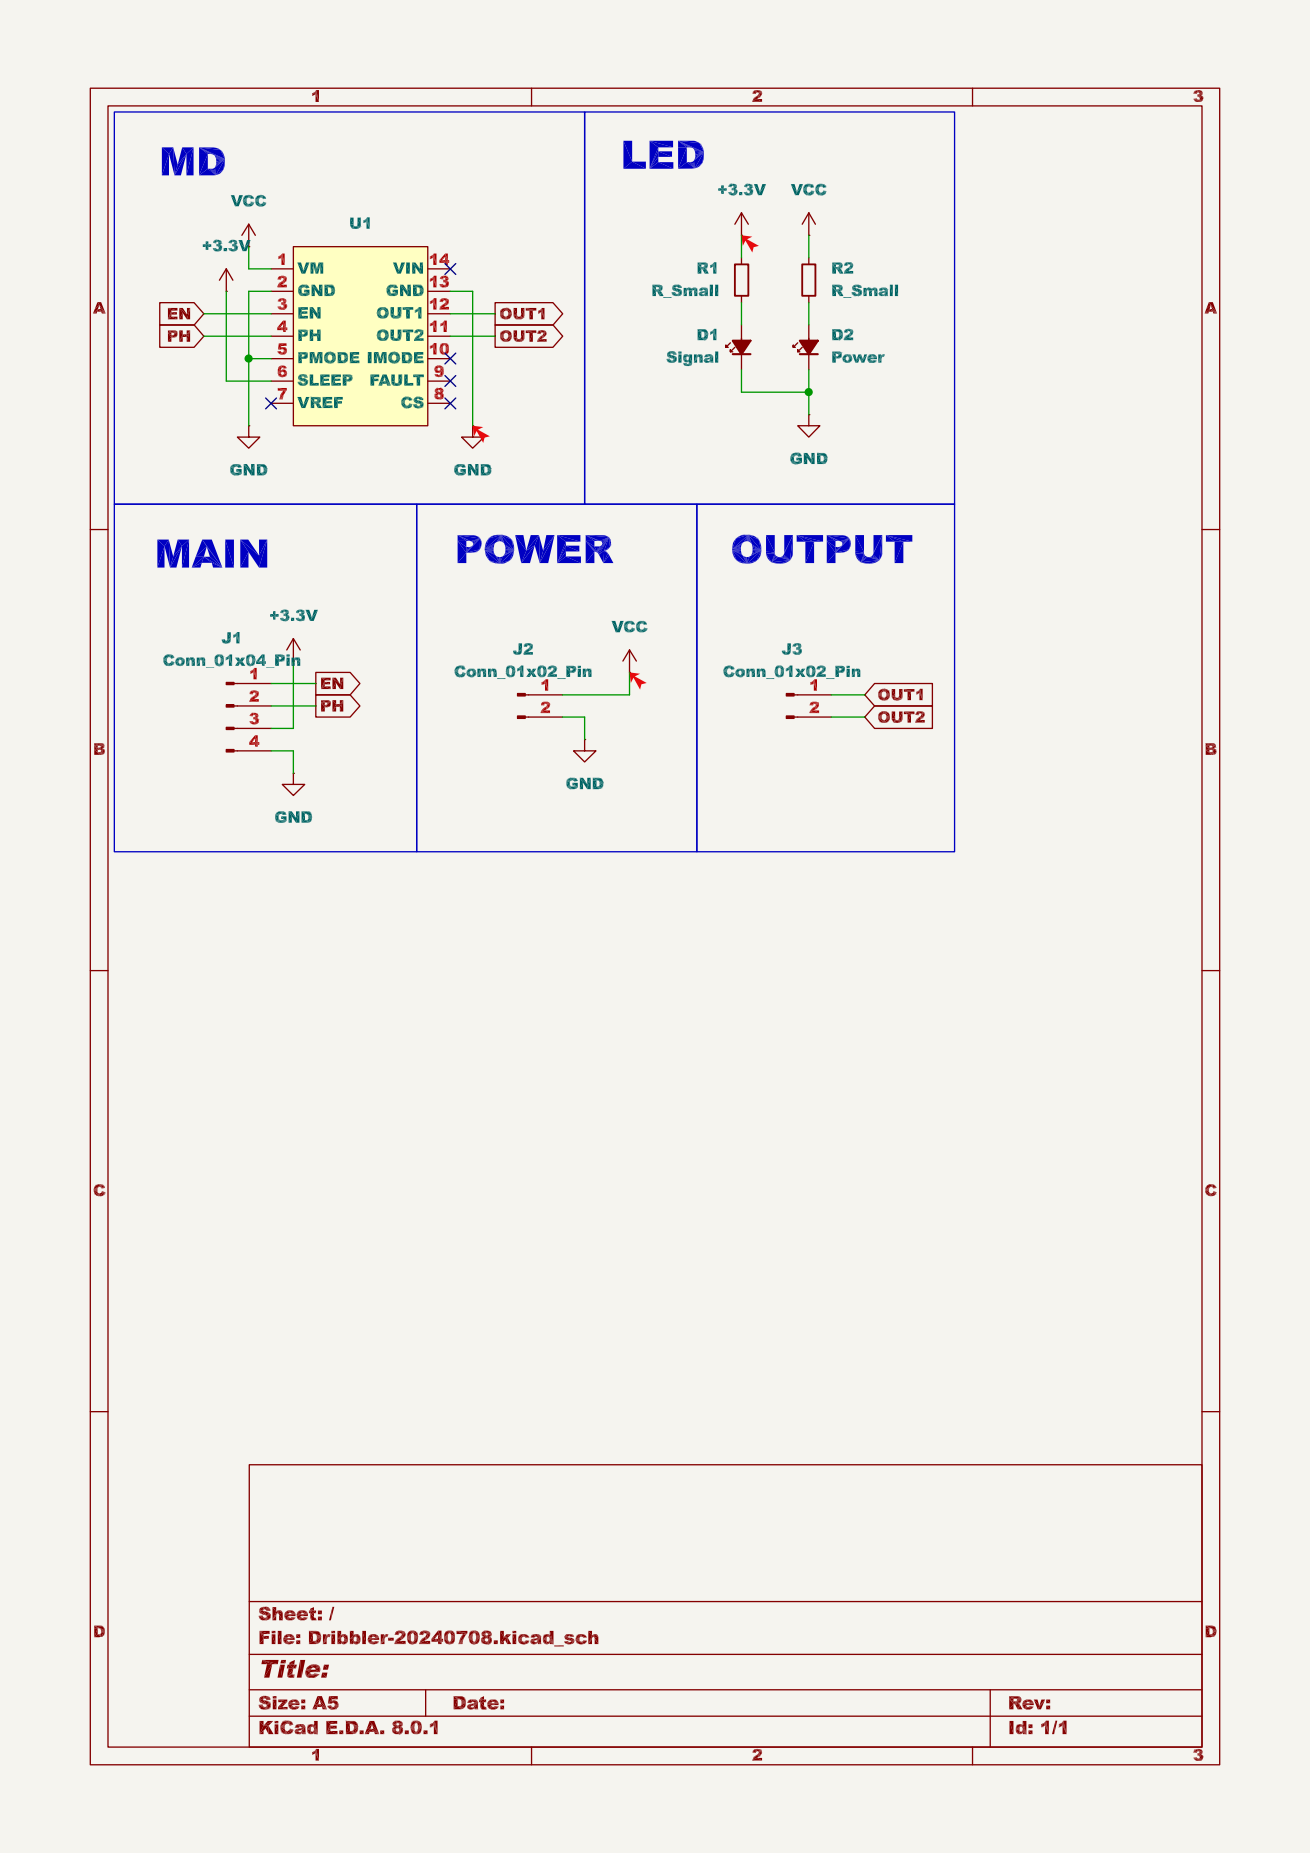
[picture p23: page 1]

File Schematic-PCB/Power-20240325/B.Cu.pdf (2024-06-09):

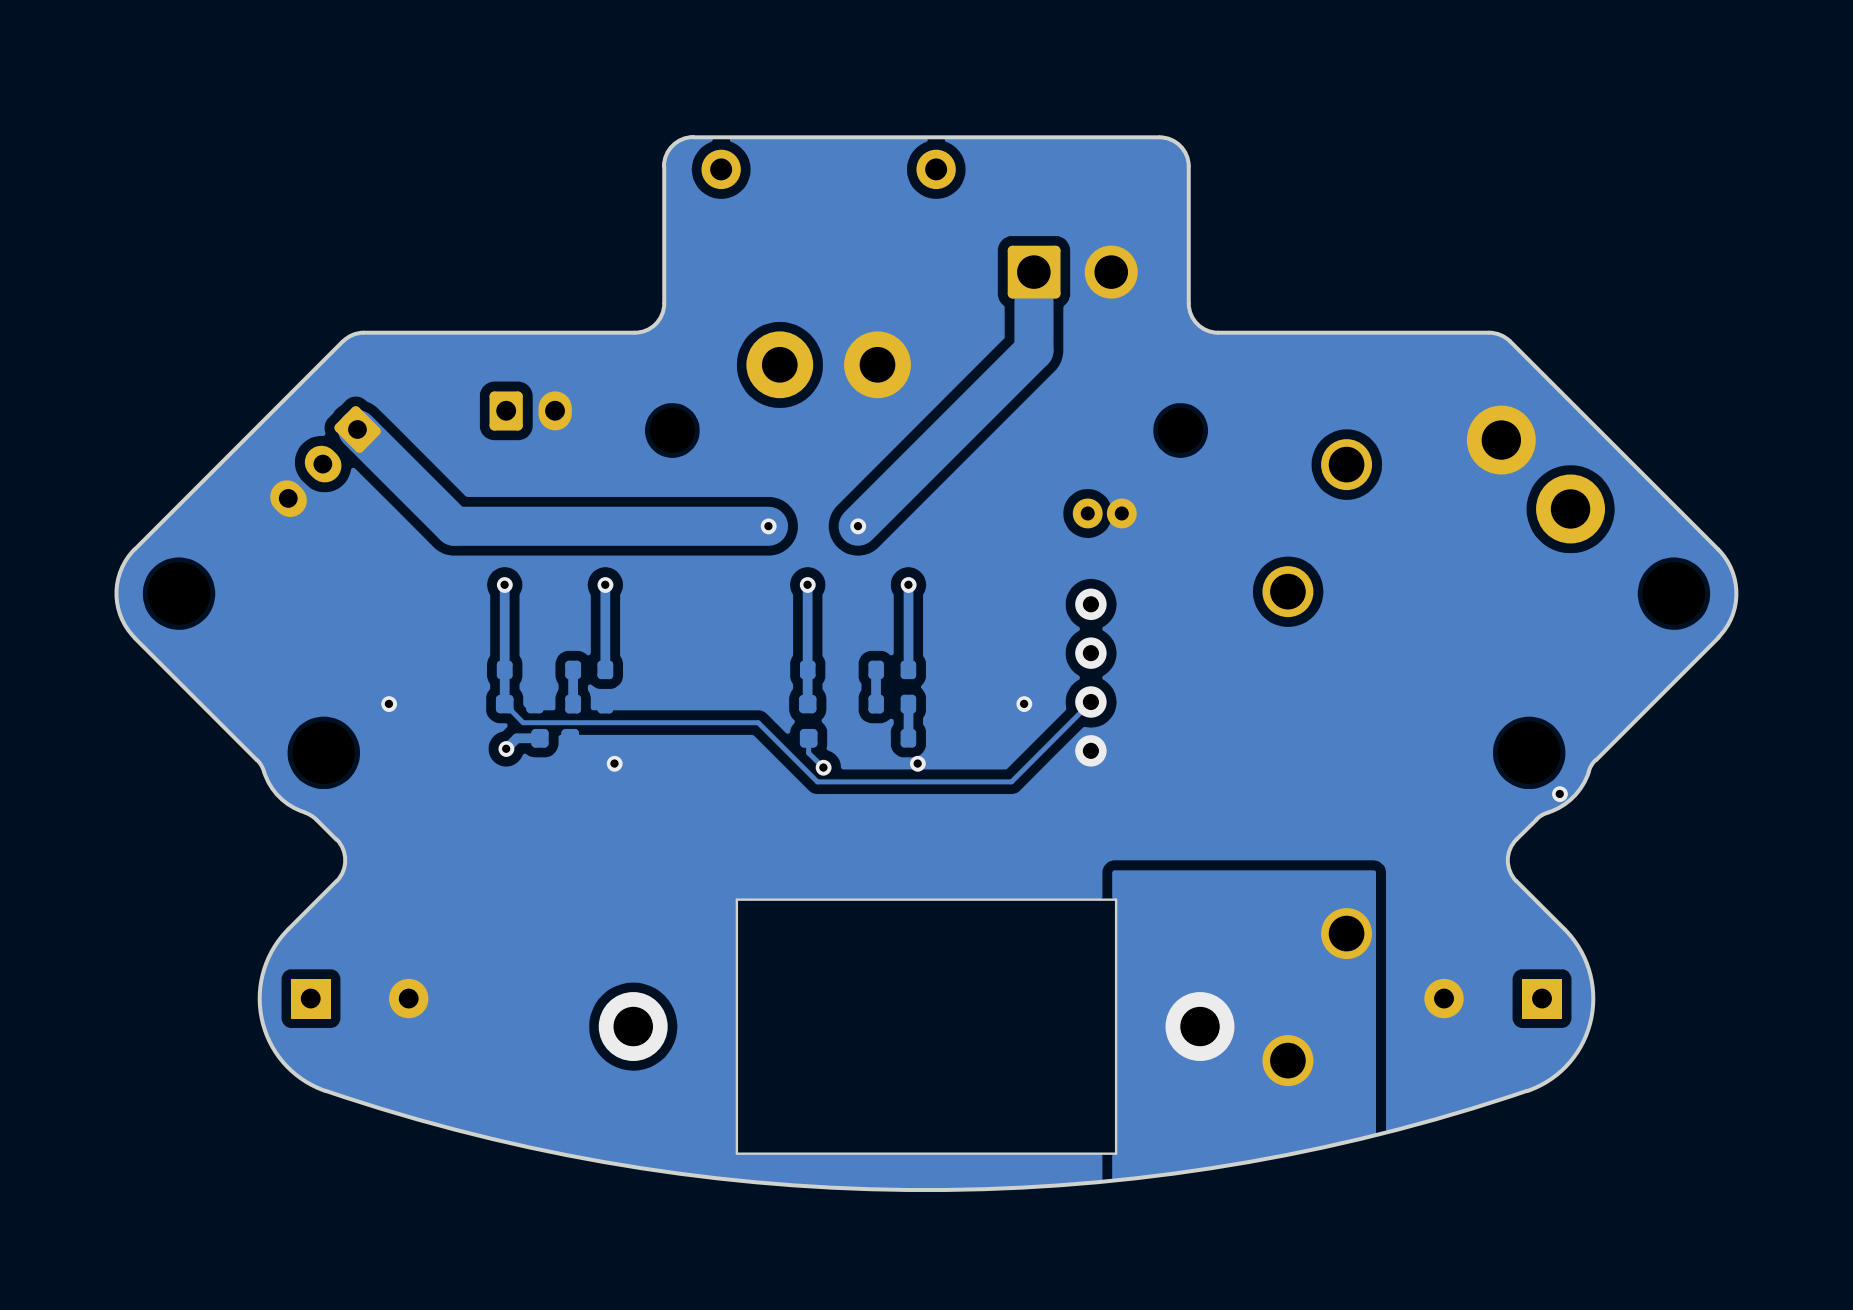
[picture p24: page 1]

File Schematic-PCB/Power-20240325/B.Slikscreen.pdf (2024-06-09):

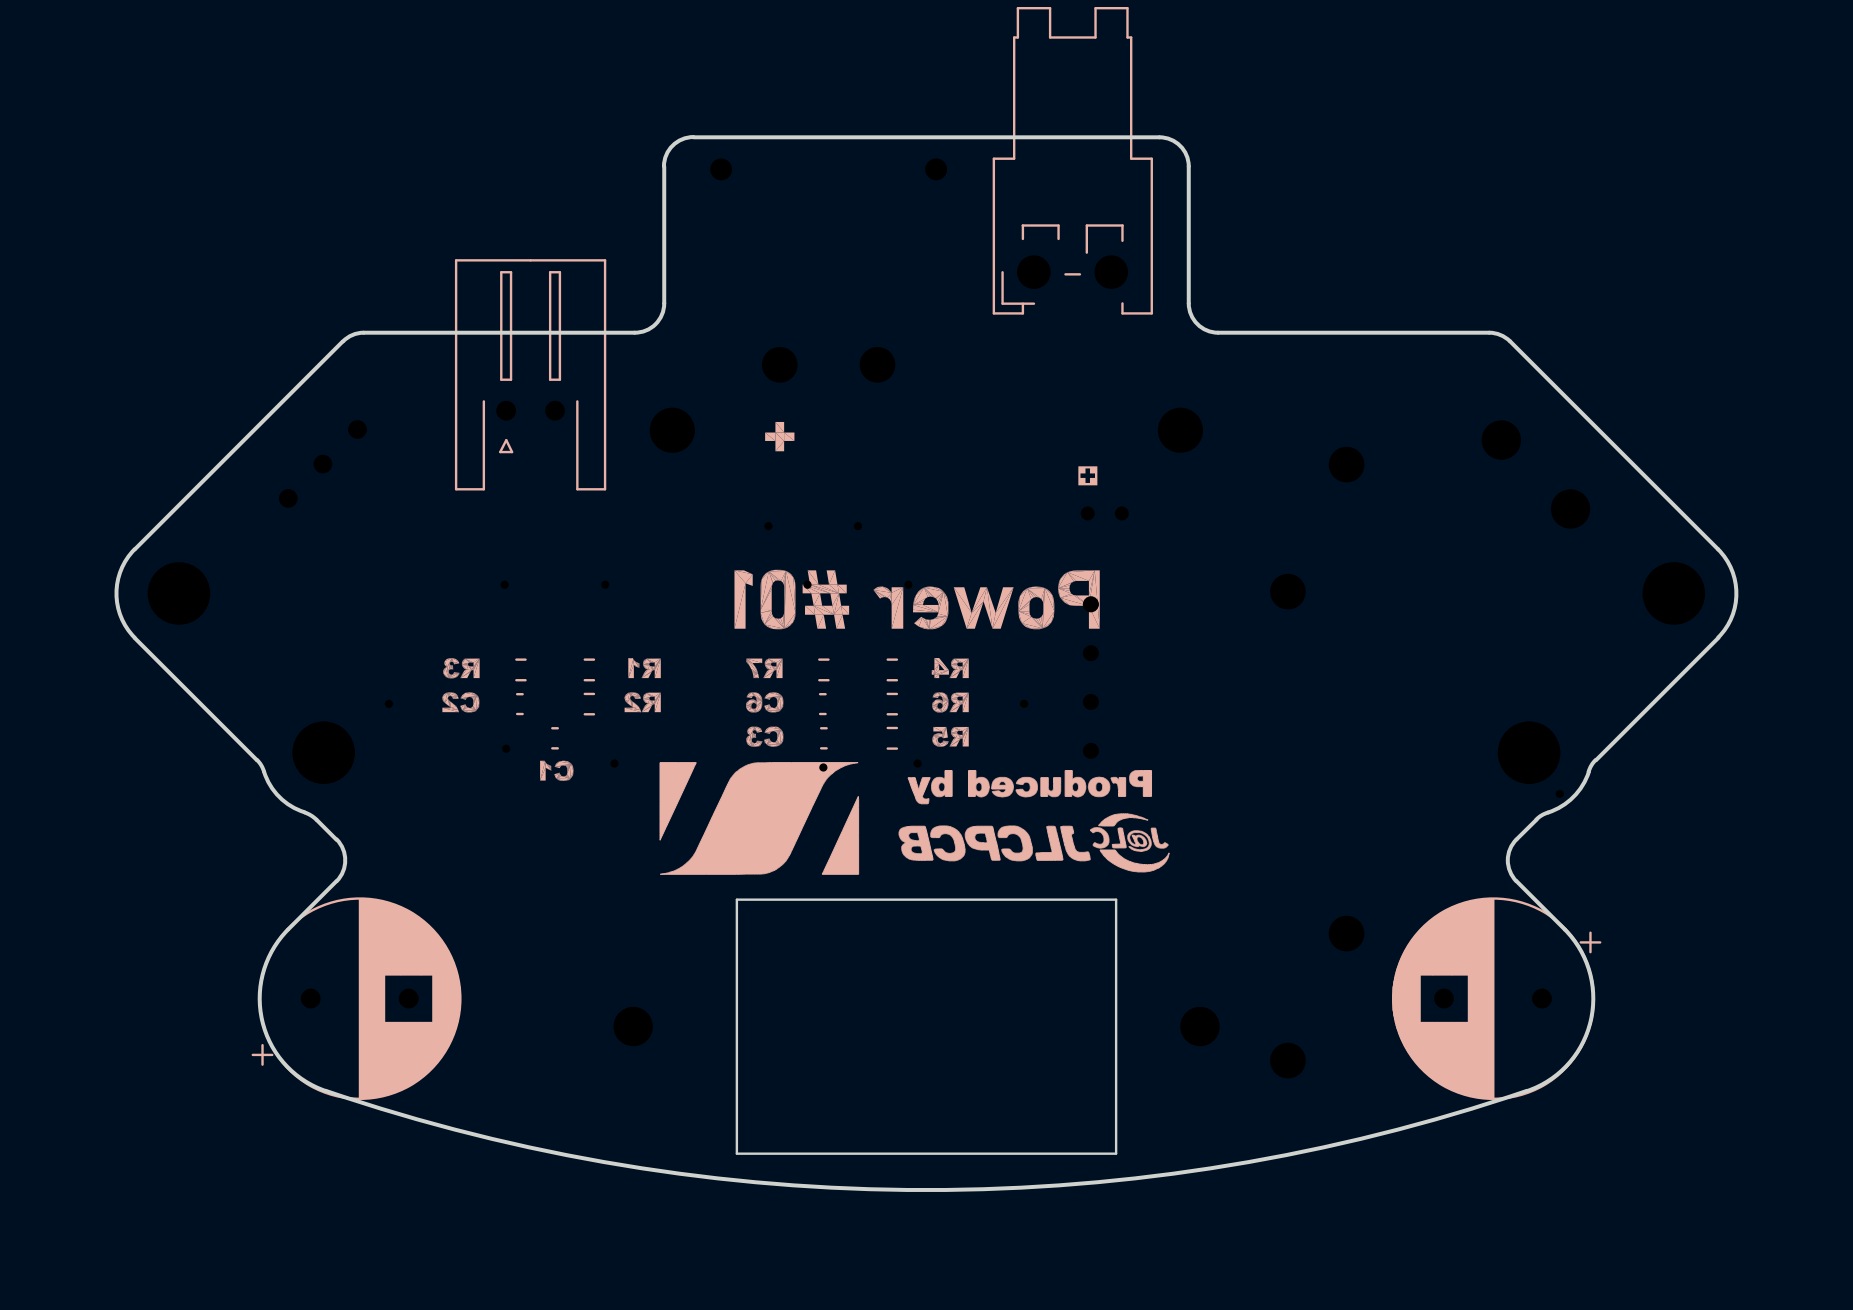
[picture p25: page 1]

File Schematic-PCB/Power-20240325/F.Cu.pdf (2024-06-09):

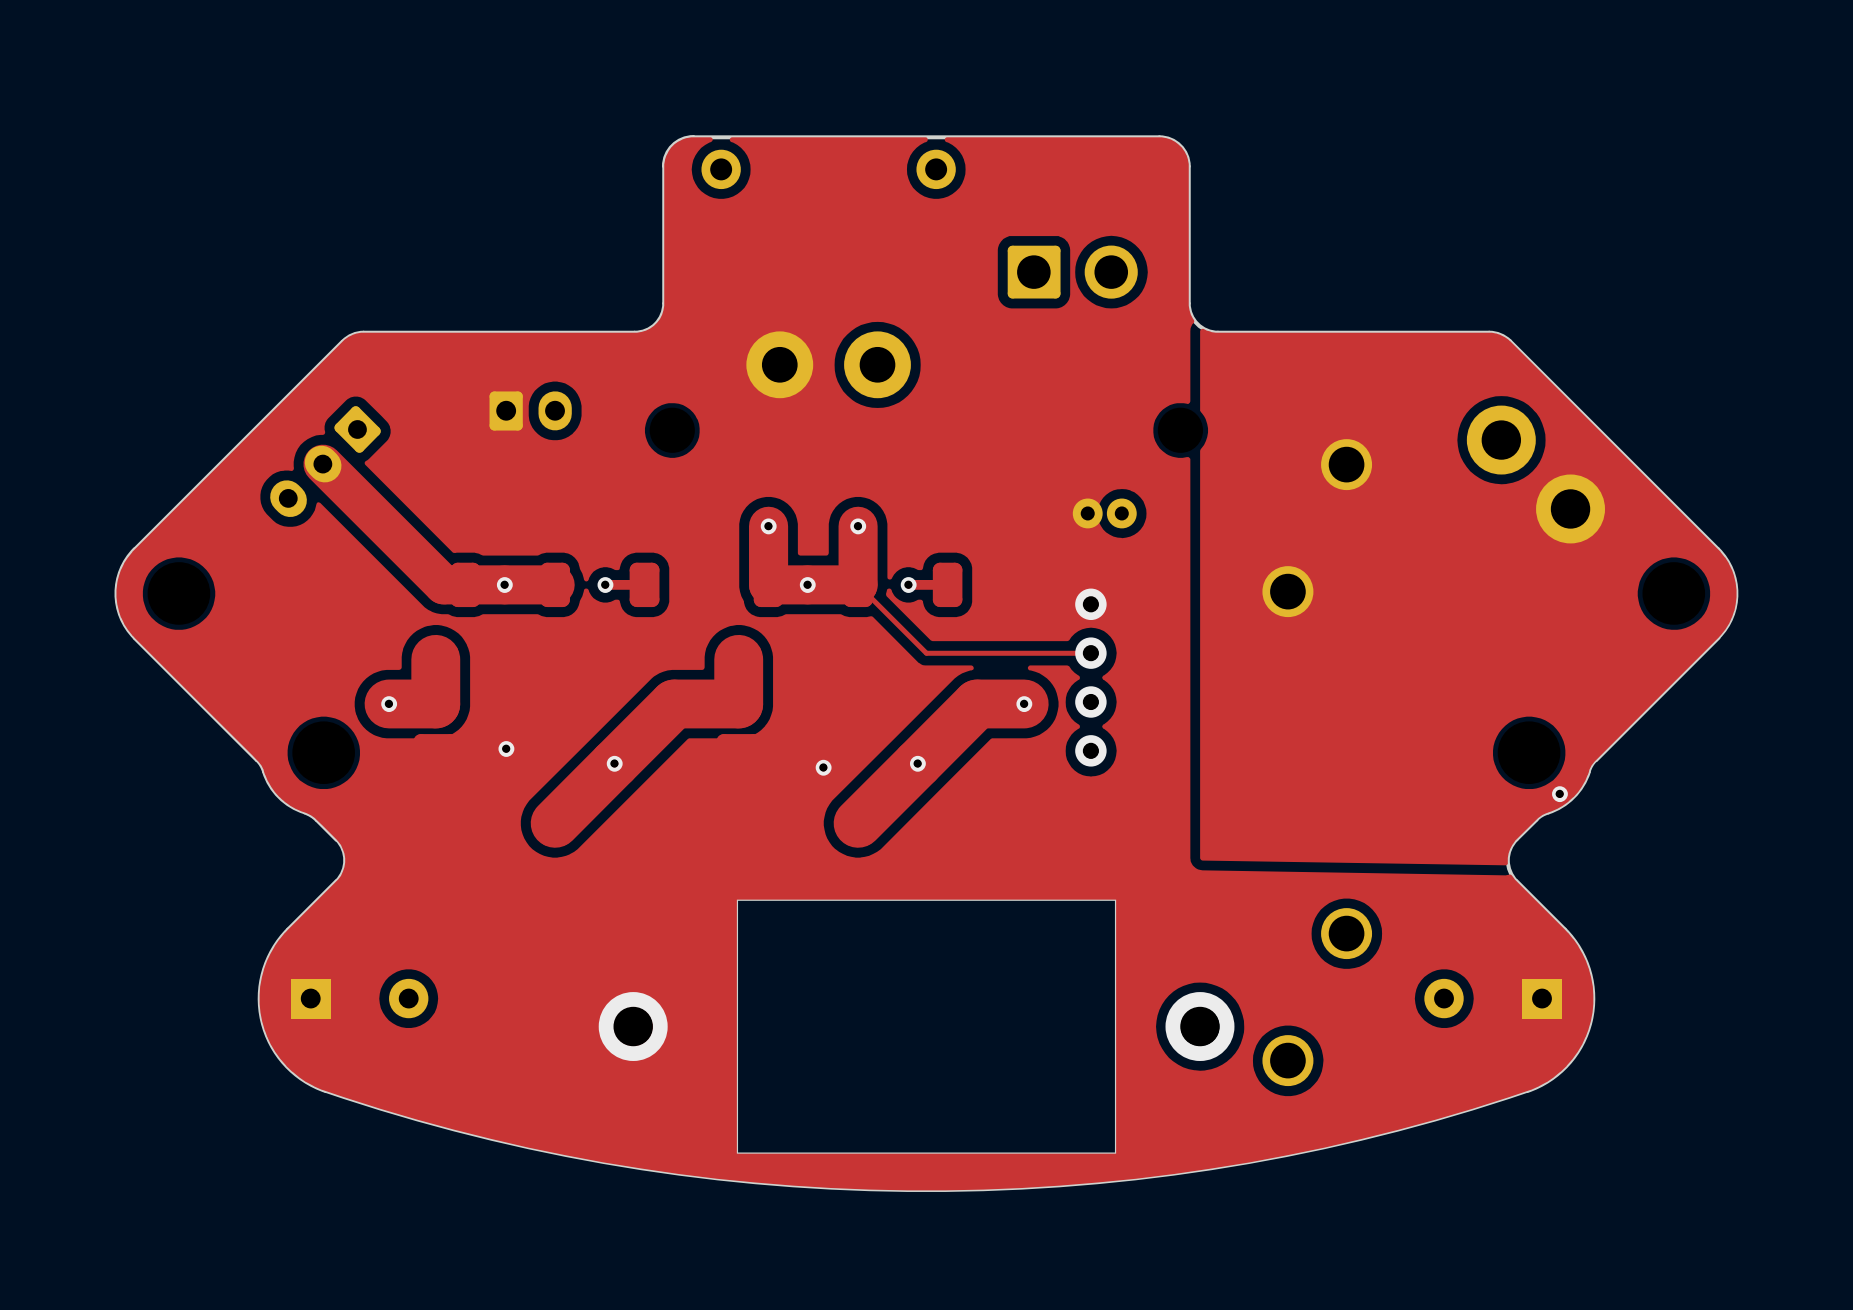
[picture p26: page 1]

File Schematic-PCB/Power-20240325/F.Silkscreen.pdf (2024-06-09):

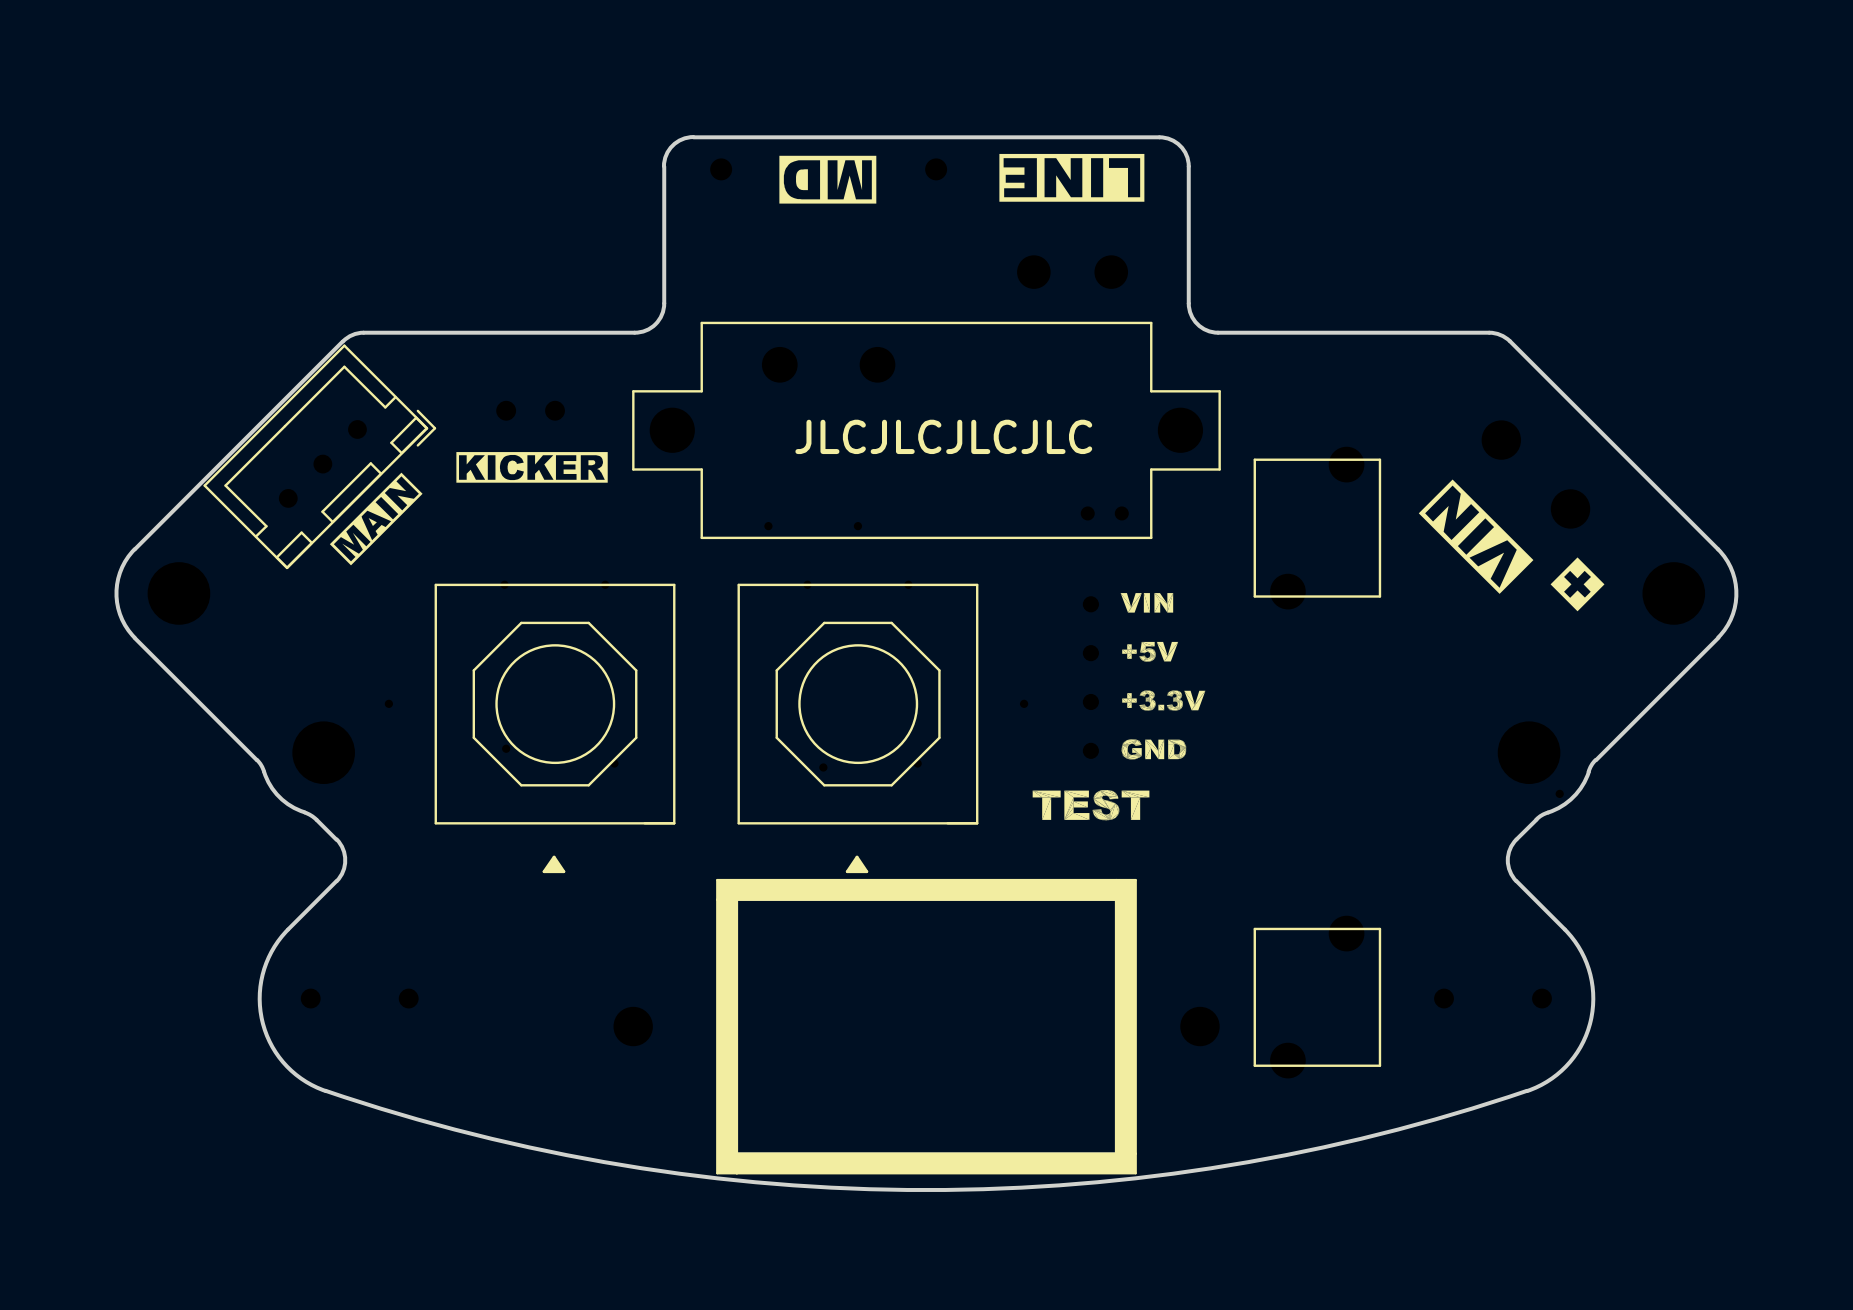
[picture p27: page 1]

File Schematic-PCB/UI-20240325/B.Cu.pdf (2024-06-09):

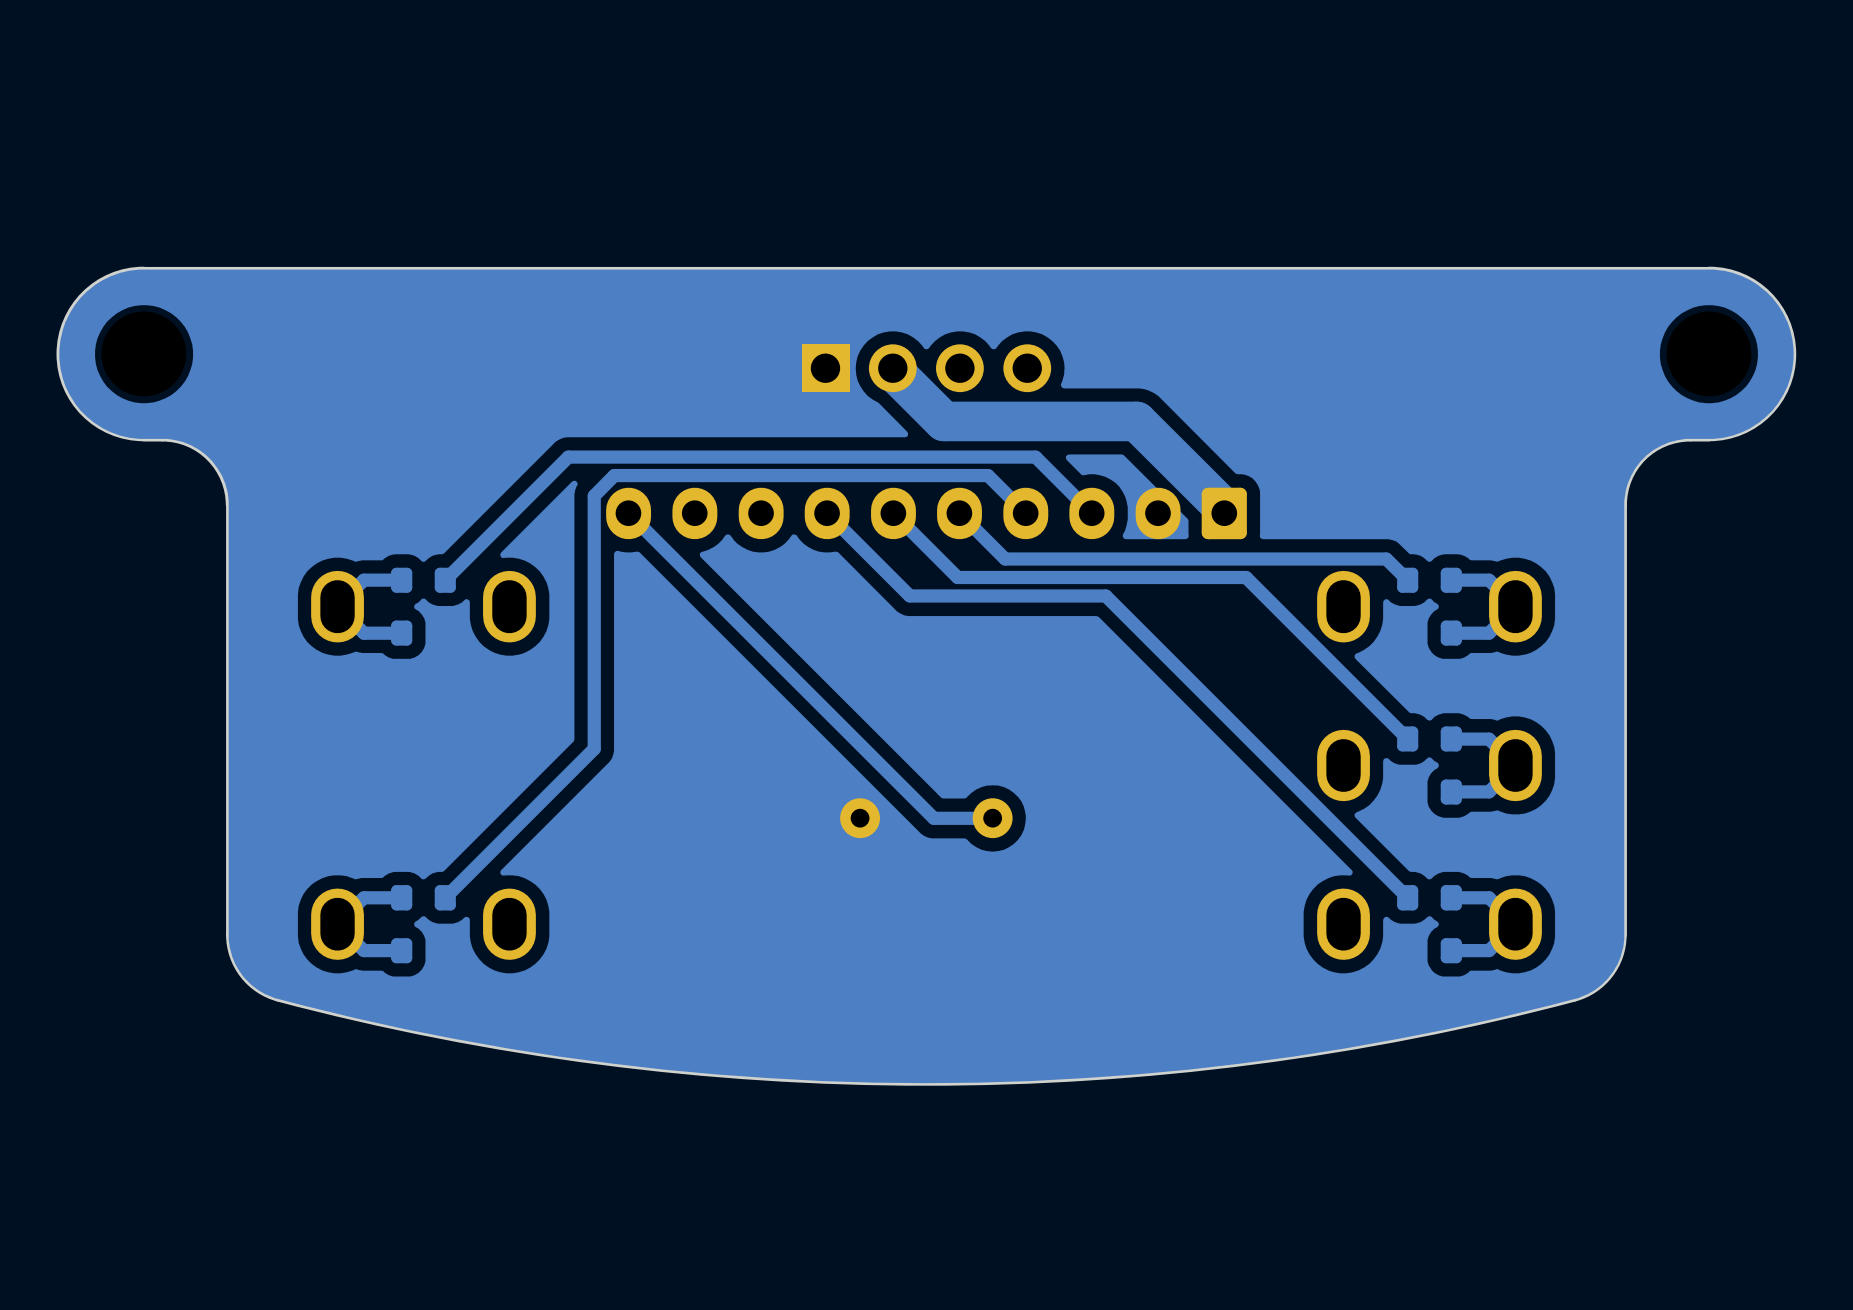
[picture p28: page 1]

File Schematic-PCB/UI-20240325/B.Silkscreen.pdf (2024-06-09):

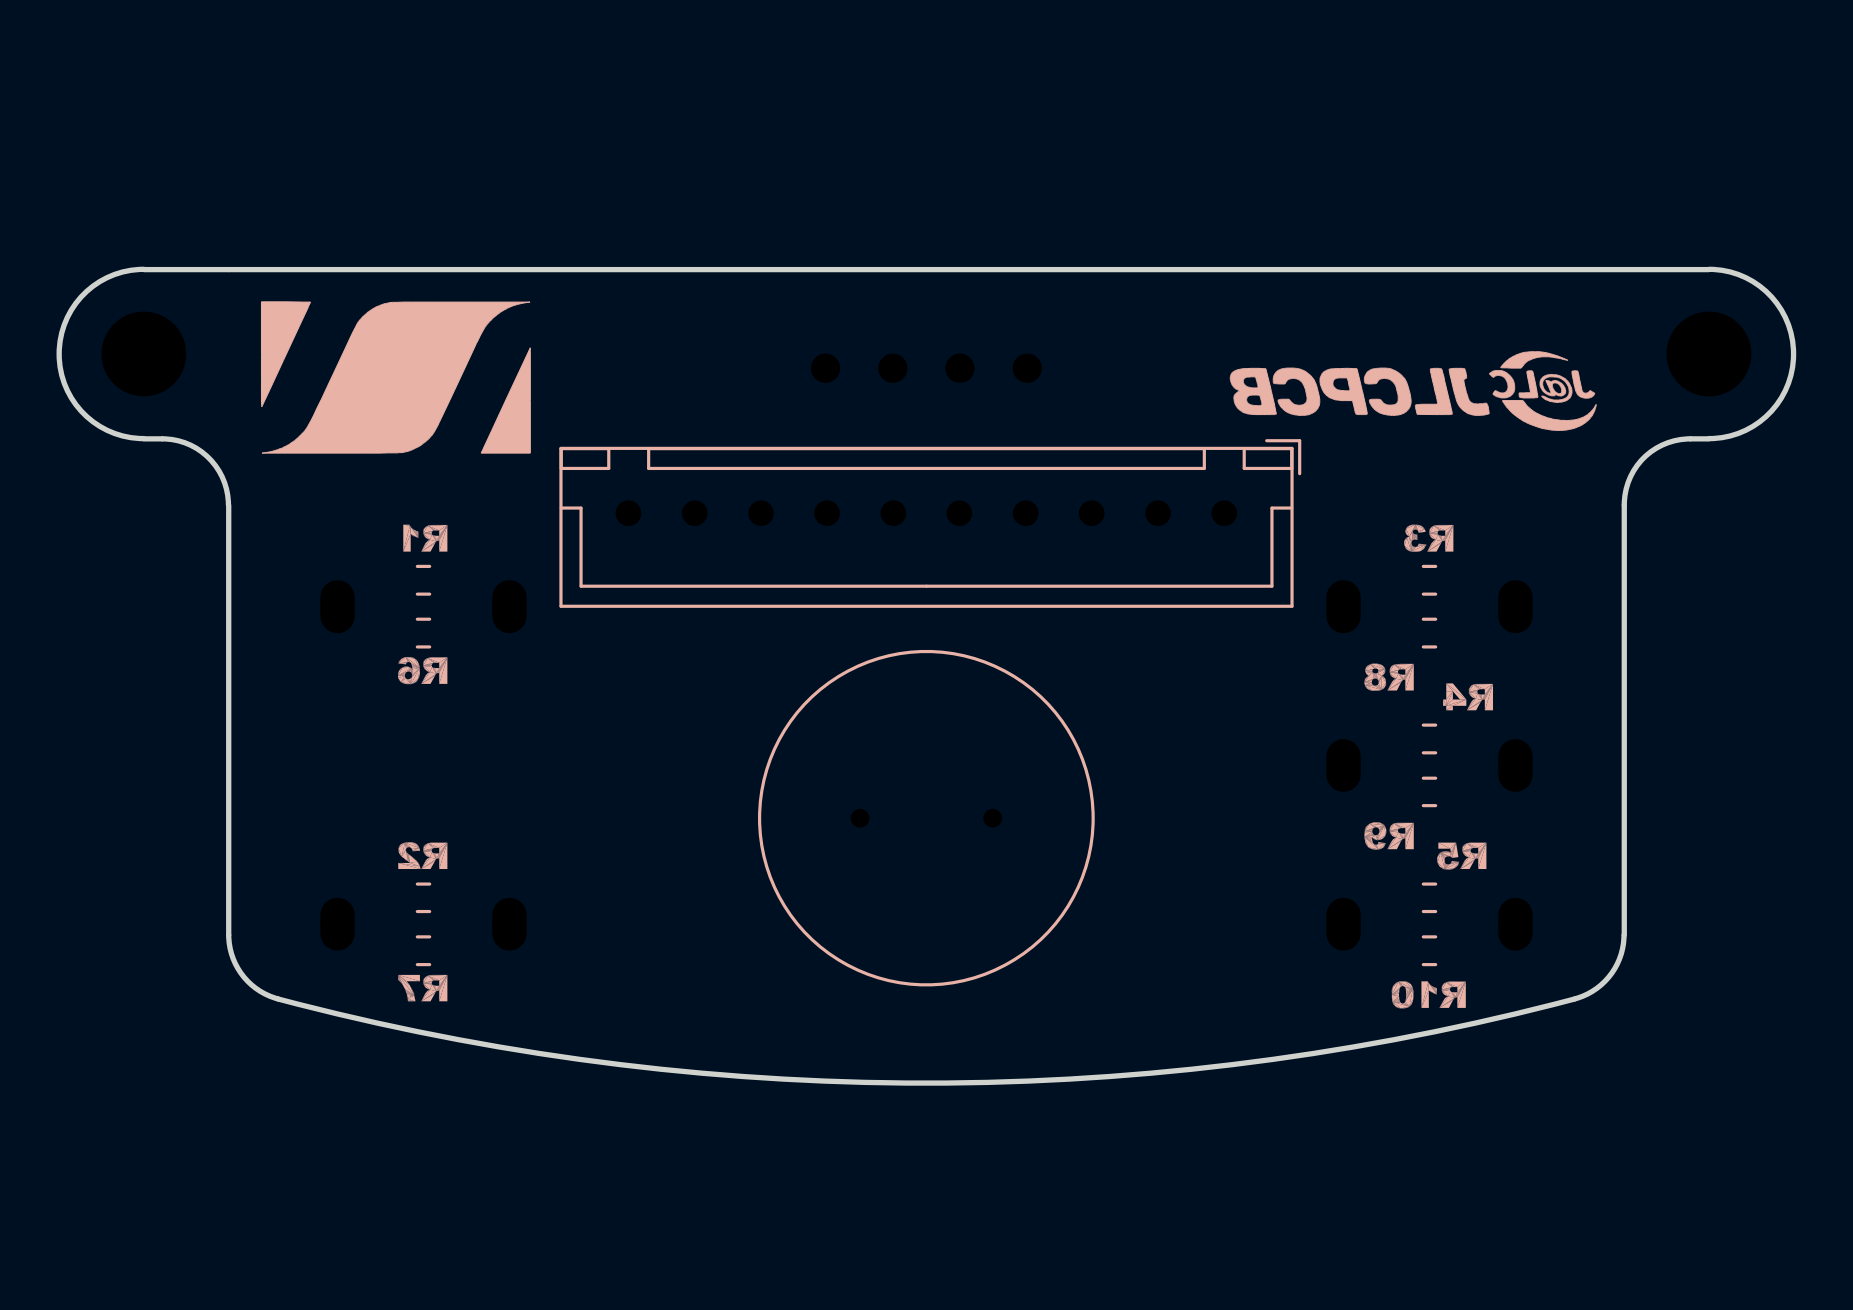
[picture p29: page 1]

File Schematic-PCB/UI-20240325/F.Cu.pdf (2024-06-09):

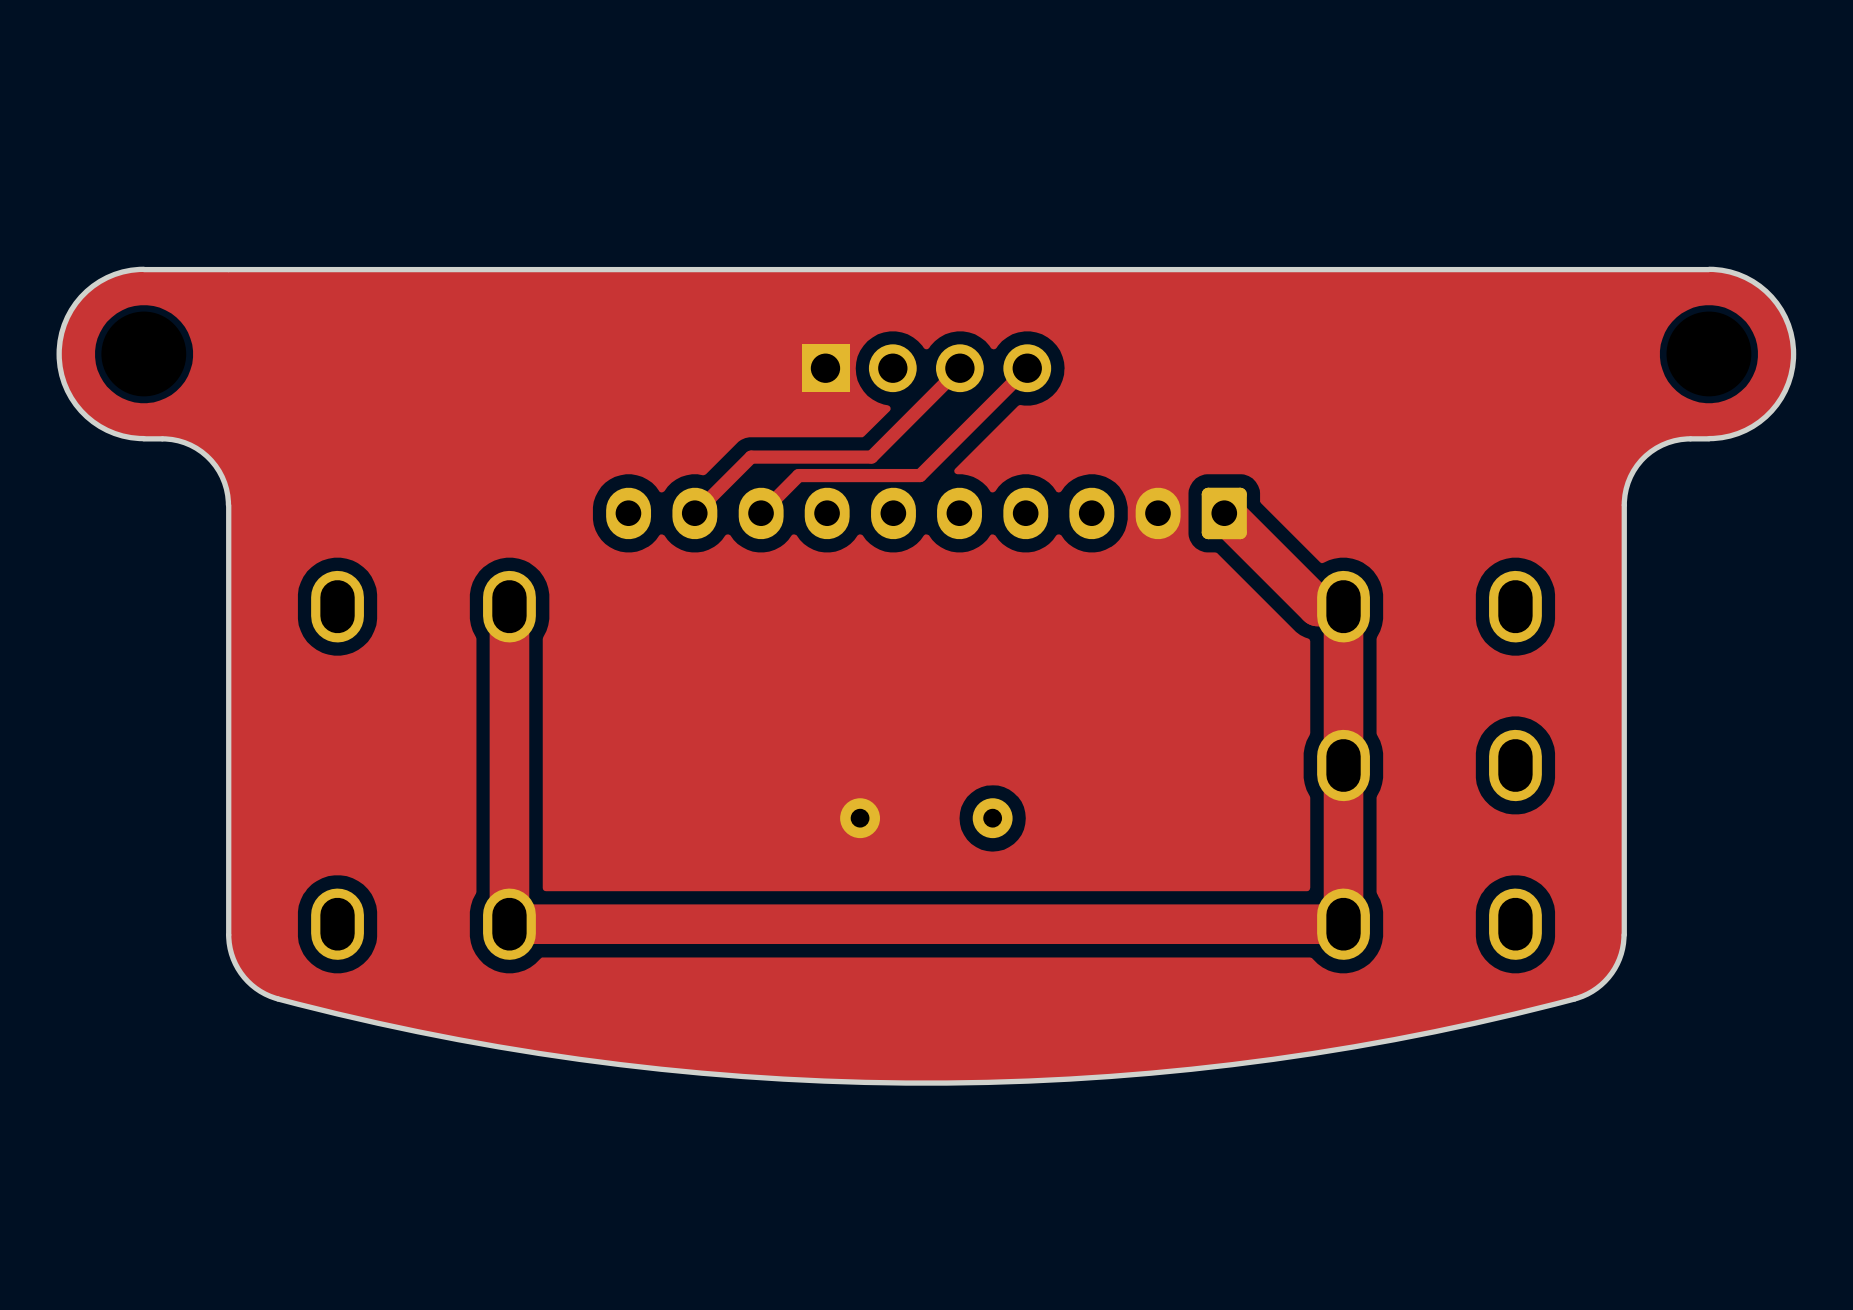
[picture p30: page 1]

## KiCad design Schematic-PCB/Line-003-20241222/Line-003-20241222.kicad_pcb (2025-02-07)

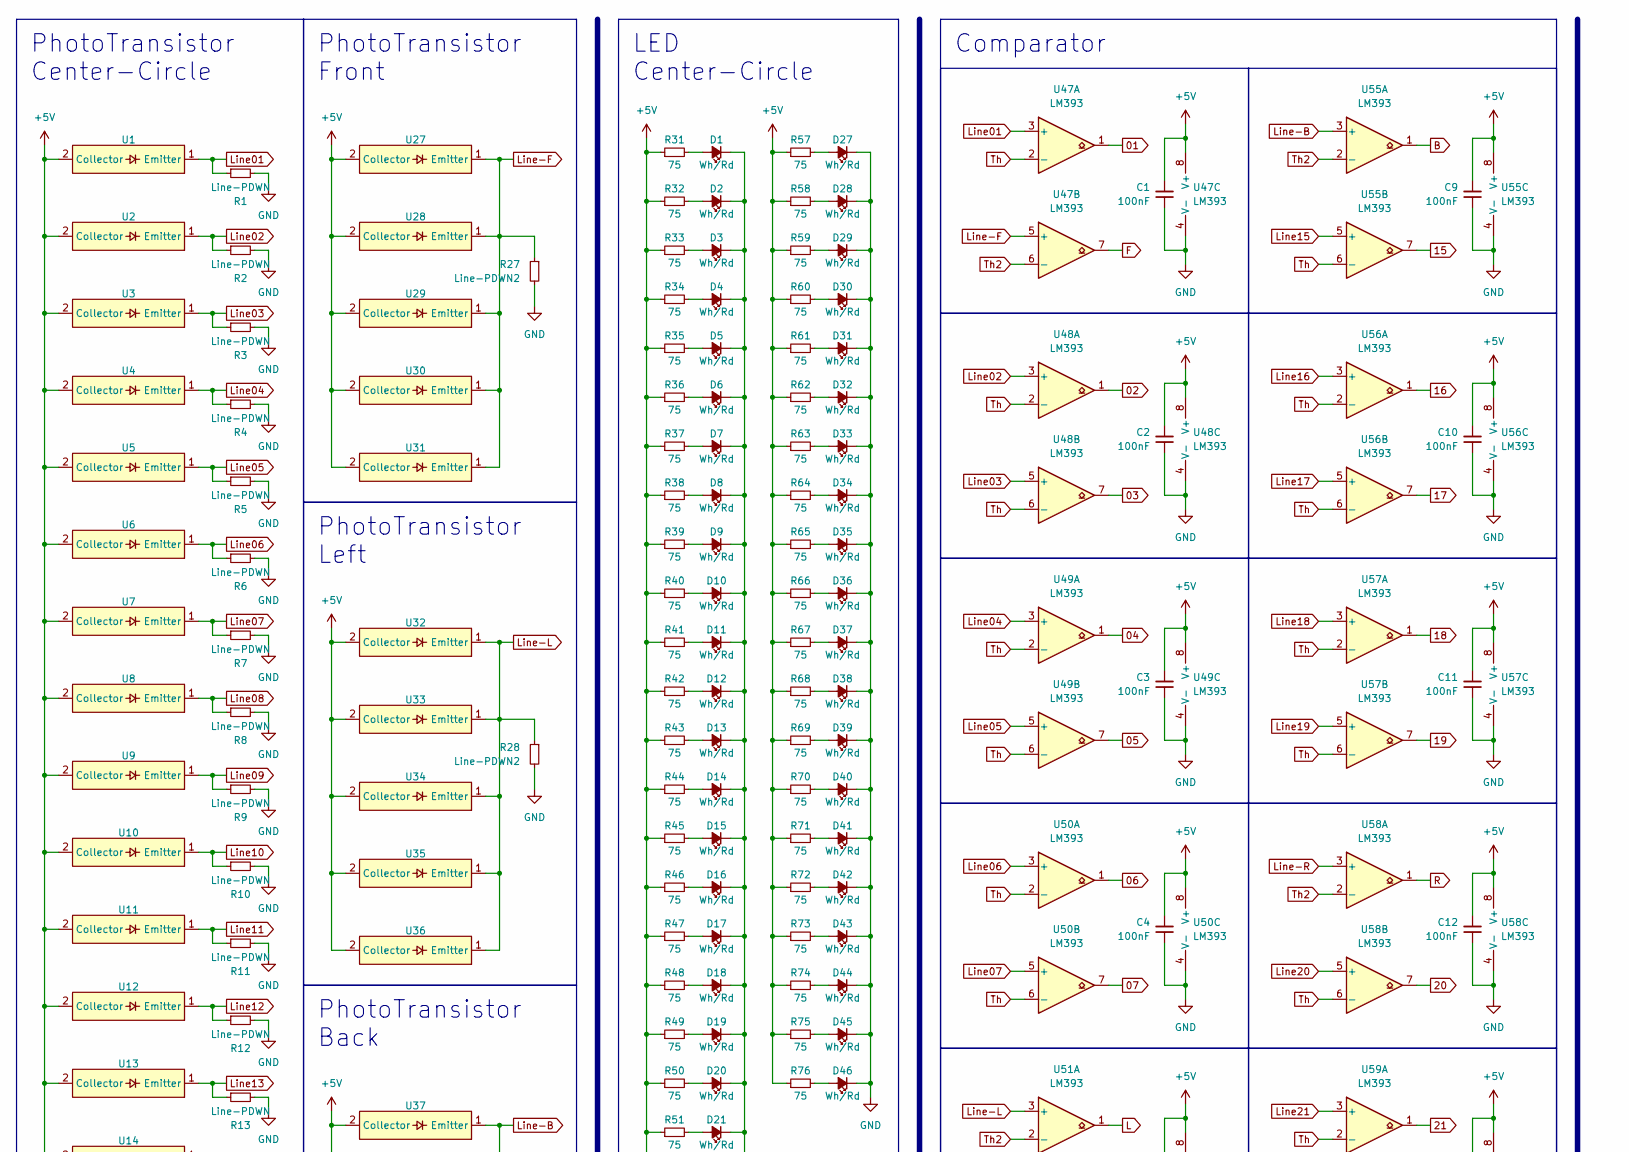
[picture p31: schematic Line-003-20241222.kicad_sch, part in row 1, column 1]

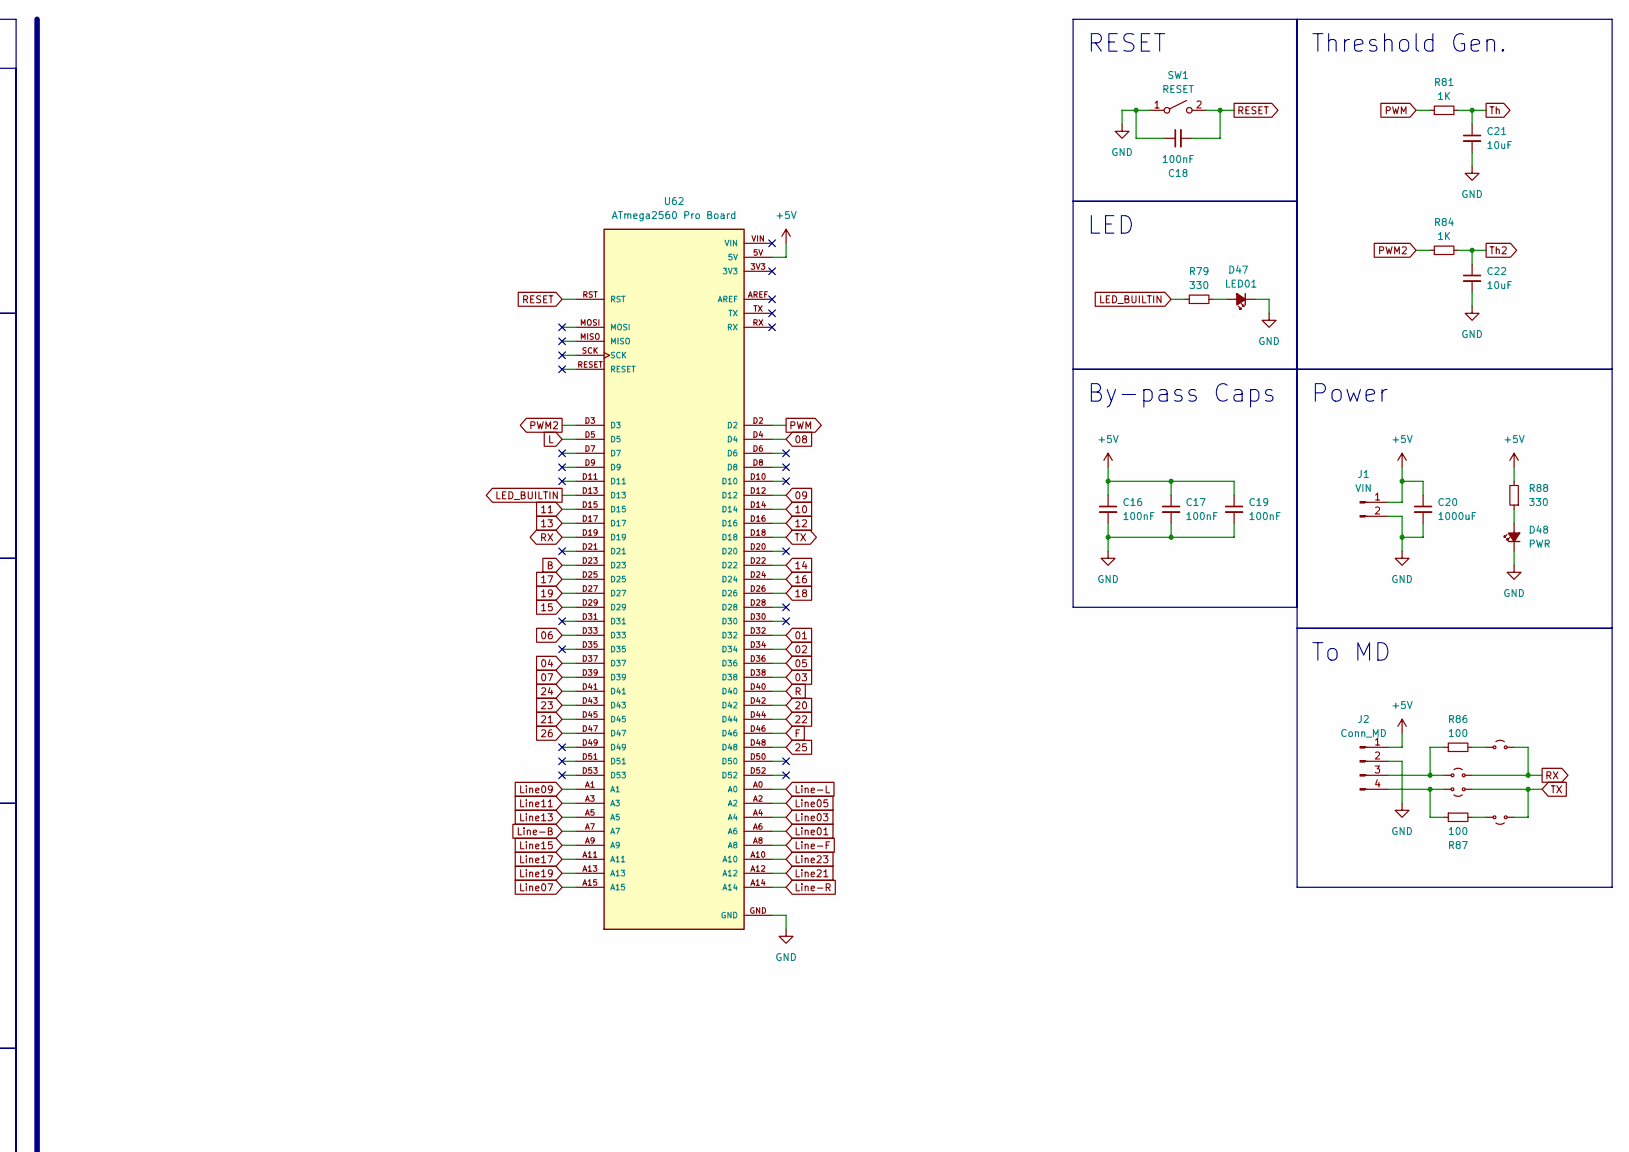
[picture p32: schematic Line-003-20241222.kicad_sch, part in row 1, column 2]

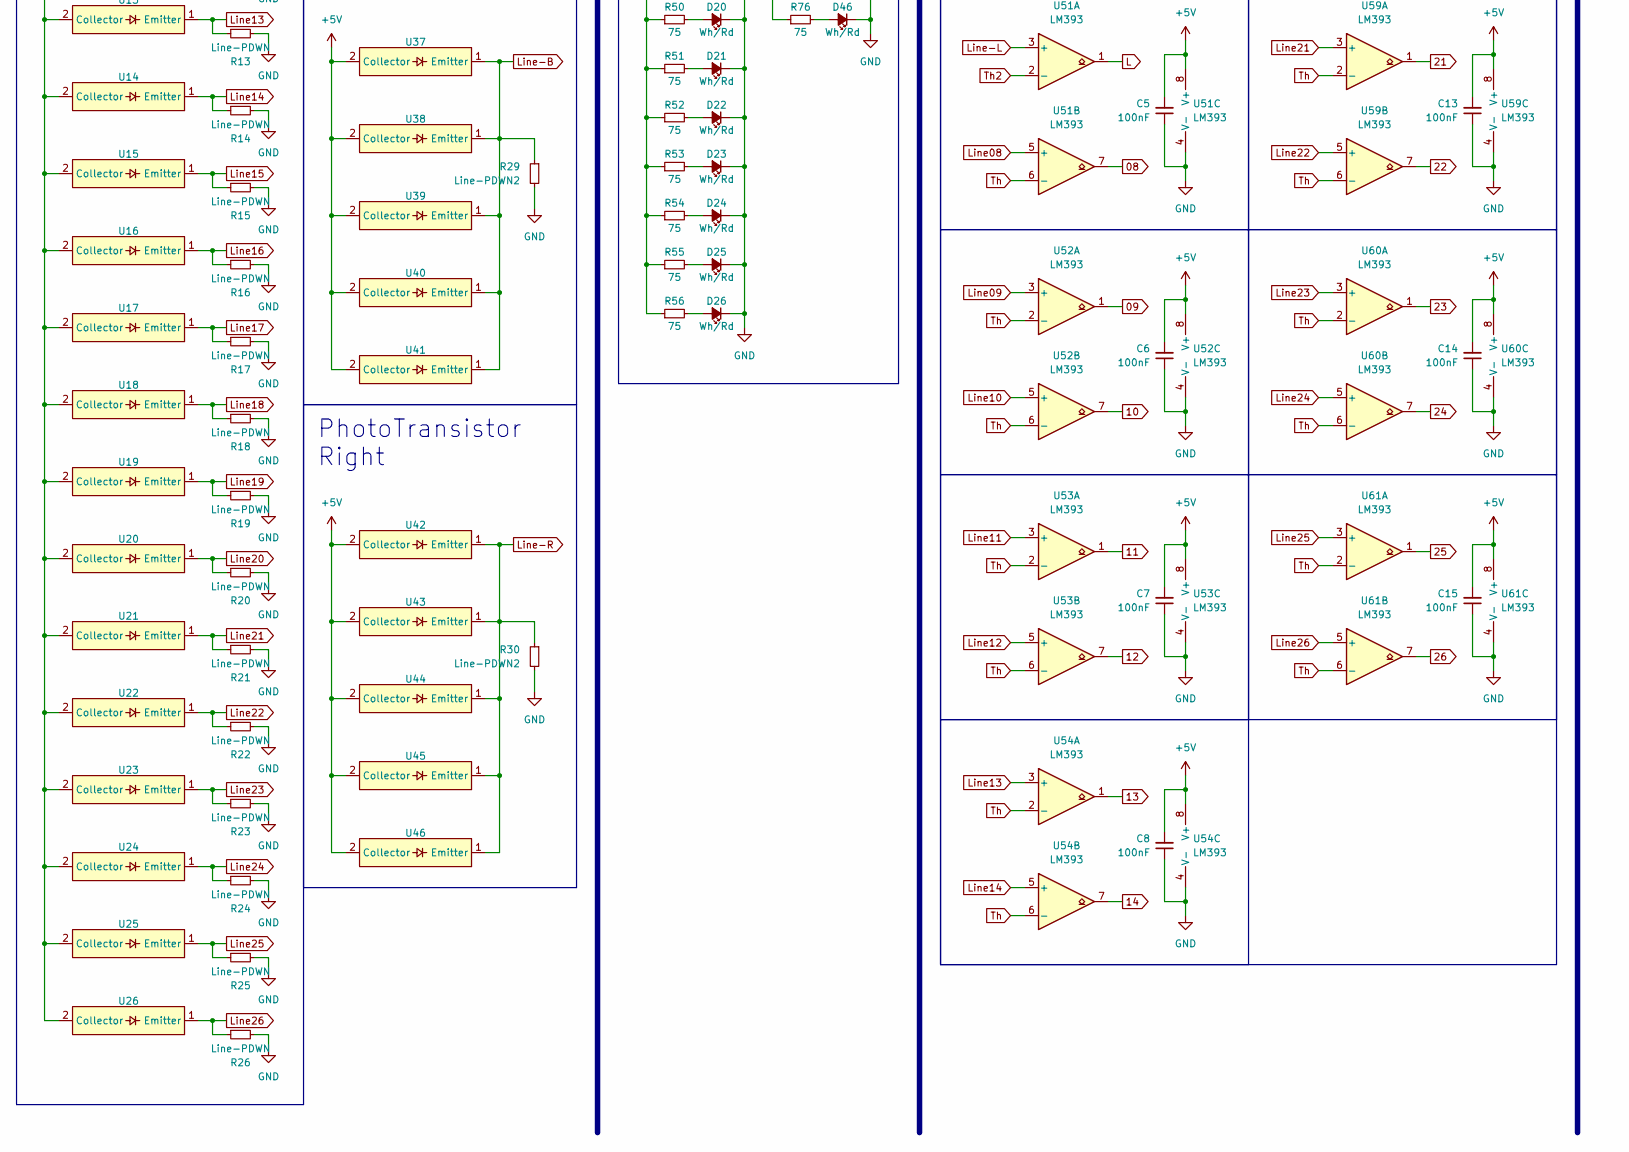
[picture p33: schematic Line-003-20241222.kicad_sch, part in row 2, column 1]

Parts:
C1, C2, C3, C4, C5, C6, C7, C8, C9, C10, C11, C12, C13, C14, C15, C16, C17, C18, C19: 100nF; C_0603_1608Metric
C20: 1000uF; CP_Radial_D10.0mm_P5.00mm
C21, C22: 10uF; C_0805_2012Metric
D1, D2, D3, D4, D5, D6, D7, D8, D9, D10, D11, D12, D13, D14, D15, D16, D17, D18, D19, D20, D21, D22, D23, D24, D25, D26, D27, D28, D29, D30, D31, D32, D33, D34, D35, D36, D37, D38, D39, D40, D41, D42, D43, D44, D45, D46: Wh/Rd; LED-3mm
D47: LED01; LED_0603_1608Metric
D48: PWR; LED_0603_1608Metric
J1: VIN; JST_XH_S2B-XH-A-1_1x02_P2.50mm_Horizontal
J2: Conn_MD; Connector-MD
JP7, JP8, JP9, JP10: Jumper_2_Small_Open; SolderJumper-2_P1.3mm_Open_Pad1.0x1.5mm
R1, R2, R3, R4, R5, R6, R7, R8, R9, R10, R11, R12, R13, R14, R15, R16, R17, R18, R19, R20, R21, R22, R23, R24, R25, R26: Line-PDWN; R_0603_1608Metric
R27, R28, R29, R30: Line-PDWN2; R_0603_1608Metric
R31, R32, R33, R34, R35, R36, R37, R38, R39, R40, R41, R42, R43, R44, R45, R46, R47, R48, R49, R50, R51, R52, R53, R54, R55, R56, R57, R58, R59, R60, R61, R62, R63, R64, R65, R66, R67, R68, R69, R70, R71, R72, R73, R74, R75, R76: 75; R_0603_1608Metric
R79, R88: 330; R_0603_1608Metric
R81, R84: 1K; R_0603_1608Metric
R86, R87: 100; R_0603_1608Metric
SW1: RESET; Tactile1
U1, U2, U3, U4, U5, U6, U7, U8, U9, U10, U11, U12, U13, U14, U15, U16, U17, U18, U19, U20, U21, U22, U23, U24, U25, U26, U27, U28, U29, U30, U31, U32, U33, U34, U35, U36, U37, U38, U39, U40, U41, U42, U43, U44, U45, U46: NJL7502L
U47, U48, U49, U50, U51, U52, U53, U54, U55, U56, U57, U58, U59, U60, U61: LM393; SOP-8_3.9x4.9mm_P1.27mm
U62: ATmega2560 Pro Board; ATmega2560Pro Board; PARTREV 12/May/2017

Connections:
01: U47.1, U62.D32
02: U48.1, U62.D34
03: U48.7, U62.D38
04: U49.1, U62.D37
05: U49.7, U62.D36
06: U50.1, U62.D33
07: U50.7, U62.D39
08: U51.7, U62.D4
09: U52.1, U62.D12
10: U52.7, U62.D14
11: U53.1, U62.D15
12: U53.7, U62.D16
13: U54.1, U62.D17
14: U54.7, U62.D22
15: U55.7, U62.D29
16: U56.1, U62.D24
17: U56.7, U62.D25
18: U57.1, U62.D26
19: U57.7, U62.D27
20: U58.7, U62.D42
21: U59.1, U62.D45
22: U59.7, U62.D44
23: U60.1, U62.D43
24: U60.7, U62.D41
25: U61.1, U62.D48
26: U61.7, U62.D47
+5V: C1.2, C2.2, C3.2, C4.2, C5.2, C6.2, C7.2, C8.2, C9.2, C10.2, C11.2, C12.2, C13.2, C14.2, C15.2, C16.1, C17.1, C19.1, C20.1, J1.1, J2.1, R31.1, R32.1, R33.1, R34.1, R35.1, R36.1, R37.1, R38.1, R39.1, R40.1, R41.1, R42.1, R43.1, R44.1, R45.1, R46.1, R47.1, R48.1, R49.1, R50.1, R51.1, R52.1, R53.1, R54.1, R55.1, R56.1, R57.1, R58.1, R59.1, R60.1, R61.1, R62.1, R63.1, R64.1, R65.1, R66.1, R67.1, R68.1, R69.1, R70.1, R71.1, R72.1, R73.1, R74.1, R75.1, R76.1, R88.2, U1.2 (Collector), U2.2 (Collector), U3.2 (Collector), U4.2 (Collector), U5.2 (Collector), U6.2 (Collector), U7.2 (Collector), U8.2 (Collector), U9.2 (Collector), U10.2 (Collector), U11.2 (Collector), U12.2 (Collector), U13.2 (Collector), U14.2 (Collector), U15.2 (Collector), U16.2 (Collector), U17.2 (Collector), U18.2 (Collector), U19.2 (Collector), U20.2 (Collector), U21.2 (Collector), U22.2 (Collector), U23.2 (Collector), U24.2 (Collector), U25.2 (Collector), U26.2 (Collector), U27.2 (Collector), U28.2 (Collector), U29.2 (Collector), U30.2 (Collector), U31.2 (Collector), U32.2 (Collector), U33.2 (Collector), U34.2 (Collector), U35.2 (Collector), U36.2 (Collector), U37.2 (Collector), U38.2 (Collector), U39.2 (Collector), U40.2 (Collector), U41.2 (Collector), U42.2 (Collector), U43.2 (Collector), U44.2 (Collector), U45.2 (Collector), U46.2 (Collector), U47.8 (V+), U48.8 (V+), U49.8 (V+), U50.8 (V+), U51.8 (V+), U52.8 (V+), U53.8 (V+), U54.8 (V+), U55.8 (V+), U56.8 (V+), U57.8 (V+), U58.8 (V+), U59.8 (V+), U60.8 (V+), U61.8 (V+), U62.5V
B: U55.1, U62.D23
F: U47.7, U62.D46
GND: C1.1, C2.1, C3.1, C4.1, C5.1, C6.1, C7.1, C8.1, C9.1, C10.1, C11.1, C12.1, C13.1, C14.1, C15.1, C16.2, C17.2, C18.1, C19.2, C20.2, C21.2, C22.2, D1.1 (K), D2.1 (K), D3.1 (K), D4.1 (K), D5.1 (K), D6.1 (K), D7.1 (K), D8.1 (K), D9.1 (K), D10.1 (K), D11.1 (K), D12.1 (K), D13.1 (K), D14.1 (K), D15.1 (K), D16.1 (K), D17.1 (K), D18.1 (K), D19.1 (K), D20.1 (K), D21.1 (K), D22.1 (K), D23.1 (K), D24.1 (K), D25.1 (K), D26.1 (K), D27.1 (K), D28.1 (K), D29.1 (K), D30.1 (K), D31.1 (K), D32.1 (K), D33.1 (K), D34.1 (K), D35.1 (K), D36.1 (K), D37.1 (K), D38.1 (K), D39.1 (K), D40.1 (K), D41.1 (K), D42.1 (K), D43.1 (K), D44.1 (K), D45.1 (K), D46.1 (K), D47.1 (K), D48.1 (K), J1.2, J2.2, R1.2, R2.2, R3.2, R4.2, R5.2, R6.2, R7.2, R8.2, R9.2, R10.2, R11.2, R12.2, R13.2, R14.2, R15.2, R16.2, R17.2, R18.2, R19.2, R20.2, R21.2, R22.2, R23.2, R24.2, R25.2, R26.2, R27.2, R28.2, R29.2, R30.2, SW1.1 (A), U47.4 (V-), U48.4 (V-), U49.4 (V-), U50.4 (V-), U51.4 (V-), U52.4 (V-), U53.4 (V-), U54.4 (V-), U55.4 (V-), U56.4 (V-), U57.4 (V-), U58.4 (V-), U59.4 (V-), U60.4 (V-), U61.4 (V-), U62.GND
L: U51.1, U62.D5
LED_BUILTIN: R79.1, U62.D13
Line01: R1.1, U1.1 (Emitter), U47.3 (+), U62.A6
Line02: R2.1, U2.1 (Emitter), U48.3 (+)
Line03: R3.1, U3.1 (Emitter), U48.5 (+), U62.A4
Line04: R4.1, U4.1 (Emitter), U49.3 (+)
Line05: R5.1, U5.1 (Emitter), U49.5 (+), U62.A2
Line06: R6.1, U6.1 (Emitter), U50.3 (+)
Line07: R7.1, U7.1 (Emitter), U50.5 (+), U62.A15
Line08: R8.1, U8.1 (Emitter), U51.5 (+)
Line09: R9.1, U9.1 (Emitter), U52.3 (+), U62.A1
Line10: R10.1, U10.1 (Emitter), U52.5 (+)
Line11: R11.1, U11.1 (Emitter), U53.3 (+), U62.A3
Line12: R12.1, U12.1 (Emitter), U53.5 (+)
Line13: R13.1, U13.1 (Emitter), U54.3 (+), U62.A5
Line14: R14.1, U14.1 (Emitter), U54.5 (+)
Line15: R15.1, U15.1 (Emitter), U55.5 (+), U62.A9
Line16: R16.1, U16.1 (Emitter), U56.3 (+)
Line17: R17.1, U17.1 (Emitter), U56.5 (+), U62.A11
Line18: R18.1, U18.1 (Emitter), U57.3 (+)
Line19: R19.1, U19.1 (Emitter), U57.5 (+), U62.A13
Line20: R20.1, U20.1 (Emitter), U58.5 (+)
Line21: R21.1, U21.1 (Emitter), U59.3 (+), U62.A12
Line22: R22.1, U22.1 (Emitter), U59.5 (+)
Line23: R23.1, U23.1 (Emitter), U60.3 (+), U62.A10
Line24: R24.1, U24.1 (Emitter), U60.5 (+)
Line25: R25.1, U25.1 (Emitter), U61.3 (+)
Line26: R26.1, U26.1 (Emitter), U61.5 (+)
Line-B: R29.1, U37.1 (Emitter), U38.1 (Emitter), U39.1 (Emitter), U40.1 (Emitter), U41.1 (Emitter), U55.3 (+), U62.A7
Line-F: R27.1, U27.1 (Emitter), U28.1 (Emitter), U29.1 (Emitter), U30.1 (Emitter), U31.1 (Emitter), U47.5 (+), U62.A8
Line-L: R28.1, U32.1 (Emitter), U33.1 (Emitter), U34.1 (Emitter), U35.1 (Emitter), U36.1 (Emitter), U51.3 (+), U62.A0
Line-R: R30.1, U42.1 (Emitter), U43.1 (Emitter), U44.1 (Emitter), U45.1 (Emitter), U46.1 (Emitter), U58.3 (+), U62.A14
unnamed: D1.2 (A), R31.2
unnamed: D2.2 (A), R32.2
unnamed: D3.2 (A), R33.2
unnamed: D4.2 (A), R34.2
unnamed: D5.2 (A), R35.2
unnamed: D6.2 (A), R36.2
unnamed: D7.2 (A), R37.2
unnamed: D8.2 (A), R38.2
unnamed: D9.2 (A), R39.2
unnamed: D10.2 (A), R40.2
unnamed: D11.2 (A), R41.2
unnamed: D12.2 (A), R42.2
unnamed: D13.2 (A), R43.2
unnamed: D14.2 (A), R44.2
unnamed: D15.2 (A), R45.2
unnamed: D16.2 (A), R46.2
unnamed: D17.2 (A), R47.2
unnamed: D18.2 (A), R48.2
unnamed: D19.2 (A), R49.2
unnamed: D20.2 (A), R50.2
unnamed: D21.2 (A), R51.2
unnamed: D22.2 (A), R52.2
unnamed: D23.2 (A), R53.2
unnamed: D24.2 (A), R54.2
unnamed: D25.2 (A), R55.2
unnamed: D26.2 (A), R56.2
unnamed: D27.2 (A), R57.2
unnamed: D28.2 (A), R58.2
unnamed: D29.2 (A), R59.2
unnamed: D30.2 (A), R60.2
unnamed: D31.2 (A), R61.2
unnamed: D32.2 (A), R62.2
unnamed: D33.2 (A), R63.2
unnamed: D34.2 (A), R64.2
unnamed: D35.2 (A), R65.2
unnamed: D36.2 (A), R66.2
unnamed: D37.2 (A), R67.2
unnamed: D38.2 (A), R68.2
unnamed: D39.2 (A), R69.2
unnamed: D40.2 (A), R70.2
unnamed: D41.2 (A), R71.2
unnamed: D42.2 (A), R72.2
unnamed: D43.2 (A), R73.2
unnamed: D44.2 (A), R74.2
unnamed: D45.2 (A), R75.2
unnamed: D46.2 (A), R76.2
unnamed: D47.2 (A), R79.2
unnamed: D48.2 (A), R88.1
unnamed: J2.3, JP7.1 (A), R86.1
unnamed: J2.4, JP8.1 (A), R87.1
unnamed: JP9.1 (A), R86.2
unnamed: JP10.1 (A), R87.2
PWM: R81.1, U62.D2
PWM2: R84.1, U62.D3
R: U58.1, U62.D40
RESET: C18.2, SW1.2 (B), U62.RST
RX: JP7.2 (B), JP9.2 (B), U62.D19
TX: JP8.2 (B), JP10.2 (B), U62.D18
Th: C21.1, R81.2, U47.2 (-), U48.2 (-), U48.6 (-), U49.2 (-), U49.6 (-), U50.2 (-), U50.6 (-), U51.6 (-), U52.2 (-), U52.6 (-), U53.2 (-), U53.6 (-), U54.2 (-), U54.6 (-), U55.6 (-), U56.2 (-), U56.6 (-), U57.2 (-), U57.6 (-), U58.6 (-), U59.2 (-), U59.6 (-), U60.2 (-), U60.6 (-), U61.2 (-), U61.6 (-)
Th2: C22.1, R84.2, U47.6 (-), U51.2 (-), U55.2 (-), U58.2 (-)

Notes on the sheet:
By-pass Caps
PhotoTransistor Back
LED Center-Circle
PhotoTransistor Front
PhotoTransistor Center-Circle
Threshold Gen.
RESET
LED
Comparator
Power
PhotoTransistor Right
PhotoTransistor Left
To MD

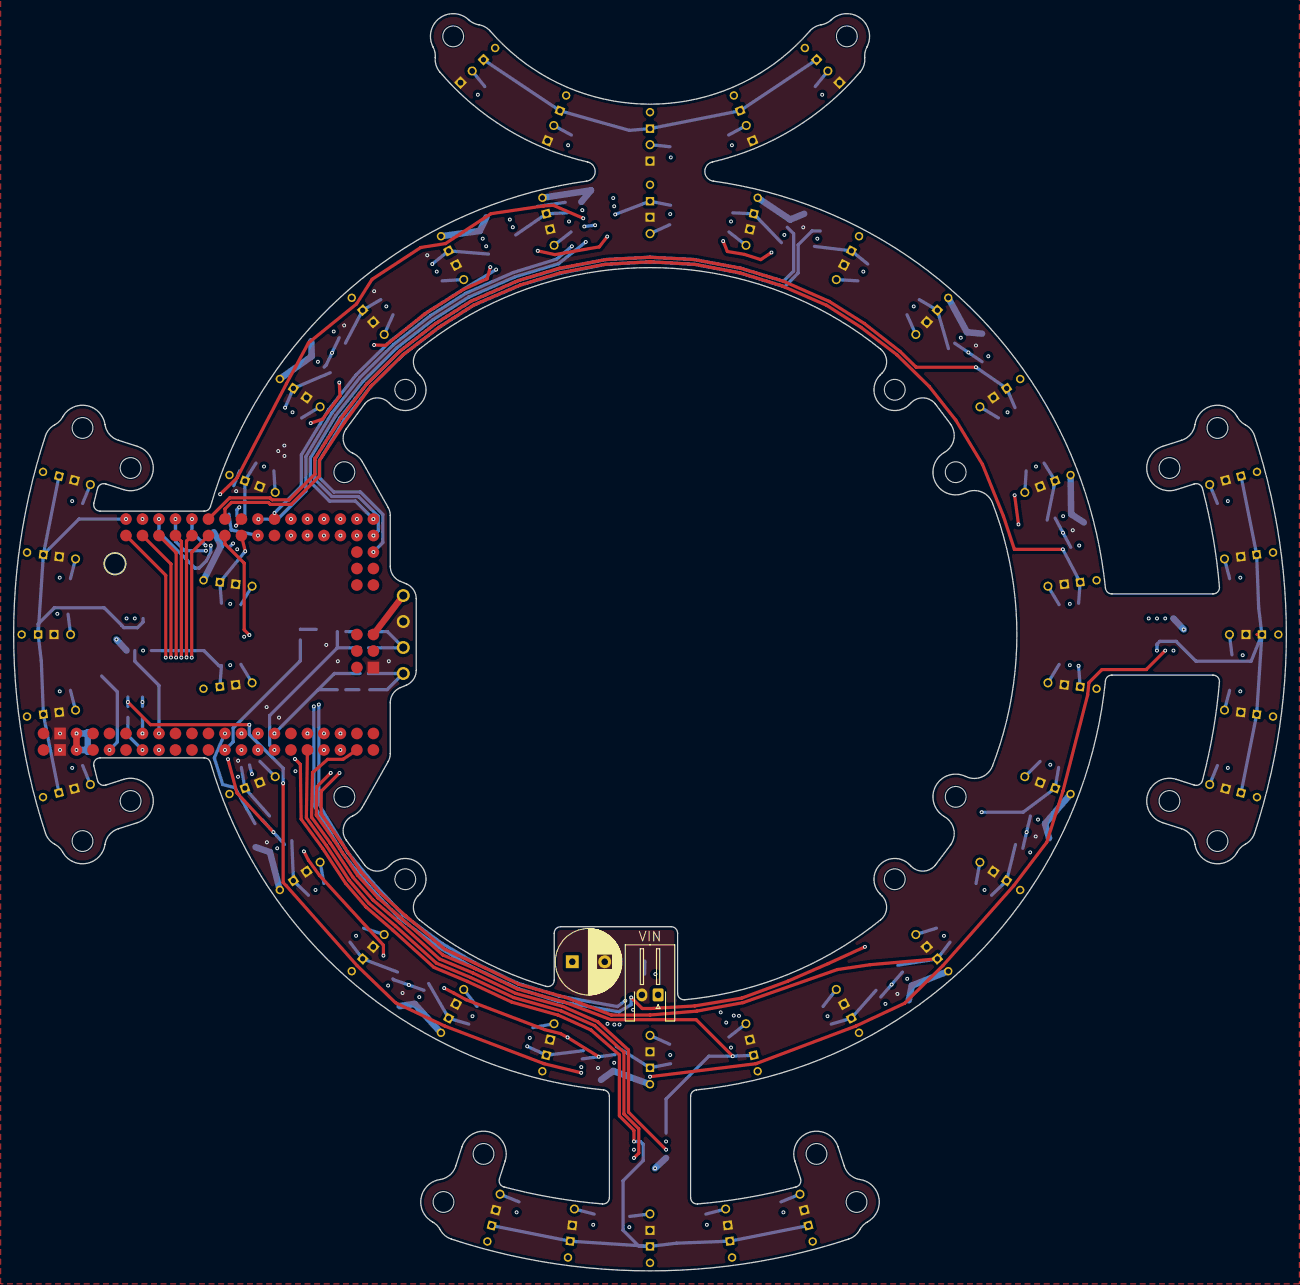
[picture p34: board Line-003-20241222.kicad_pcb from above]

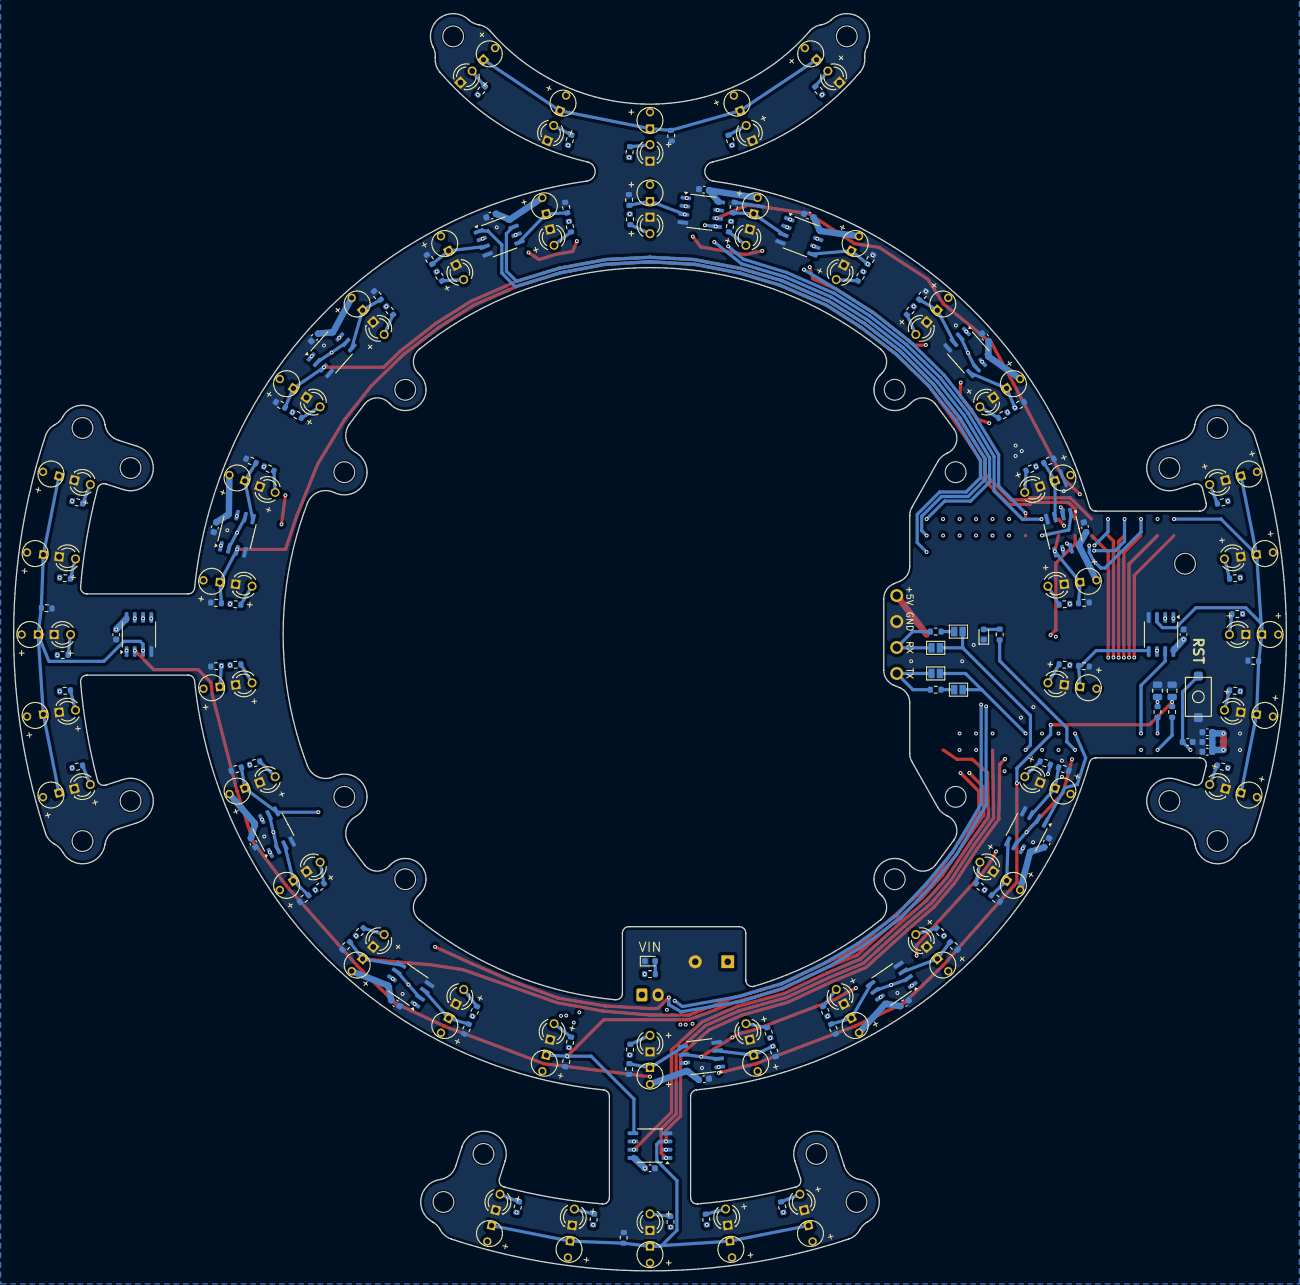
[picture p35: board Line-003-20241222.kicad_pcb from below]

Board: 4 copper layers, 196.0 x 193.6 mm, 221 parts (217 on the bottom side), 122 nets.

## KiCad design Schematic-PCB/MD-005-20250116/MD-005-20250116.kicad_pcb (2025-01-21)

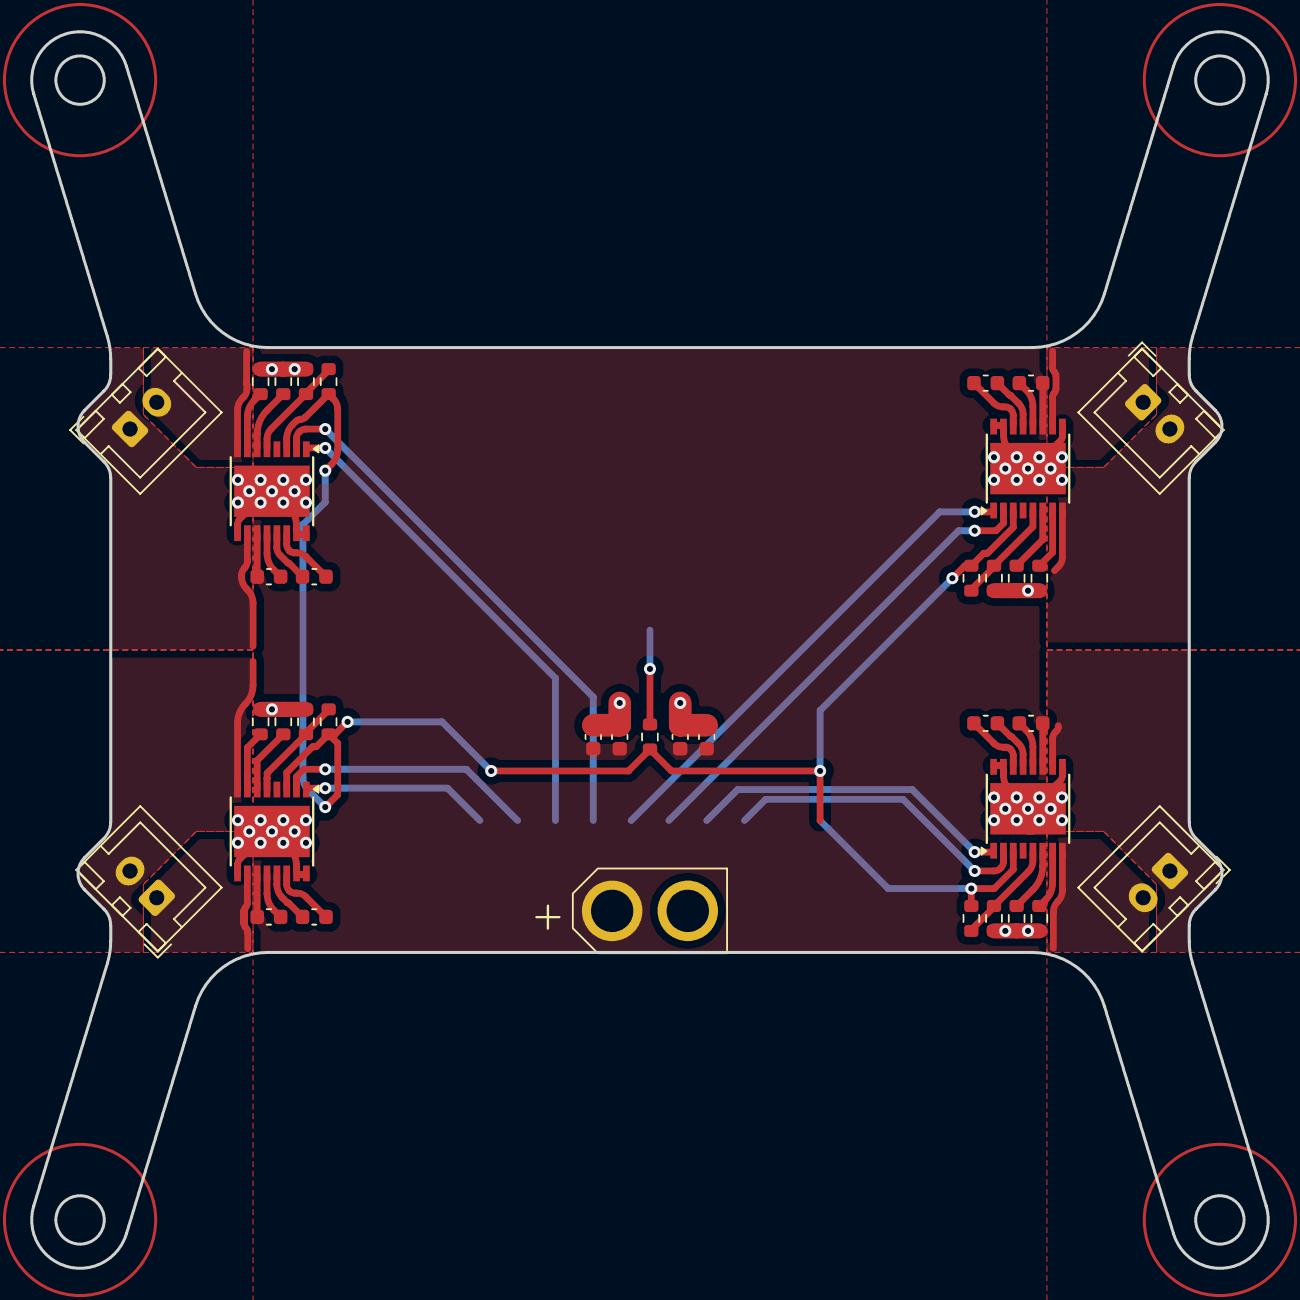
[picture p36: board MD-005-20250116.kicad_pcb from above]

Board: 2 copper layers, 81.8 x 81.8 mm, 39 parts (1 on the bottom side), 36 nets.

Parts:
C1, C2: 4.7u; C_0603_1608Metric
C3, C4: 0.1u; C_0603_1608Metric
C5, C6, C9, C10: 22n; C_0603_1608Metric
C7, C8, C11, C12: 220n; C_0603_1608Metric
D1: PWR; LED_0805_2012Metric
J1: Conn_PWR; XT30U-M
J3, J4, J5, J6: Conn_01x02_Pin; JST_XH_B2B-XH-A_1x02_P2.50mm_Vertical
R1, R2, R10, R11: 2.49k; R_0603_1608Metric
R3: 330; R_0603_1608Metric
R4, R6, R12, R14: 10k; R_0603_1608Metric
R5, R7, R13, R15: NP; R_0603_1608Metric
R8, R9, R16, R17: 20k; R_0603_1608Metric
U1, U2, U3, U4: HTSSOP-16-1EP_4.4x5mm_P0.65mm_EP3.4x5mm

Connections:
GND: C1.2, C2.2, C3.2, C4.2, D1.1 (K), J1.2, R1.2, R2.2, R5.2, R7.2, R8.2, R9.2, R10.2, R11.2, R13.2, R15.2, R16.2, R17.2, U1.9 (PGND), U1.15 (GND), U1.16 (PMODE), U1.17 (GND), U2.9 (PGND), U2.15 (GND), U2.16 (PMODE), U2.17 (GND), U3.9 (PGND), U3.15 (GND), U3.16 (PMODE), U3.17 (GND), U4.9 (PGND), U4.15 (GND), U4.16 (PMODE), U4.17 (GND)
IMODE-1: R8.1, U1.7 (IMODE)
IMODE-2: R16.1, U2.7 (IMODE)
IMODE-3: R9.1, U3.7 (IMODE)
IMODE-4: R17.1, U4.7 (IMODE)
unnamed: D1.2 (A), R3.2
unnamed: C5.2, U1.13 (CPH)
unnamed: C5.1, U1.14 (CPL)
unnamed: R1.1, U1.6 (IPROPI)
unnamed: C7.1, U1.12 (VCP)
unnamed: C6.2, U2.13 (CPH)
unnamed: C6.1, U2.14 (CPL)
unnamed: R2.1, U2.6 (IPROPI)
unnamed: C8.1, U2.12 (VCP)
unnamed: C9.2, U3.13 (CPH)
unnamed: C9.1, U3.14 (CPL)
unnamed: R10.1, U3.6 (IPROPI)
unnamed: C11.1, U3.12 (VCP)
unnamed: C10.2, U4.13 (CPH)
unnamed: C10.1, U4.14 (CPL)
unnamed: R11.1, U4.6 (IPROPI)
unnamed: C12.1, U4.12 (VCP)
OUT1-1: J3.2, U1.8 (OUT1)
OUT1-2: J4.2, U2.8 (OUT1)
OUT1-3: J5.2, U3.8 (OUT1)
OUT1-4: J6.2, U4.8 (OUT1)
OUT2-1: J3.1, U1.10 (OUT2)
OUT2-2: J4.1, U2.10 (OUT2)
OUT2-3: J5.1, U3.10 (OUT2)
OUT2-4: J6.1, U4.10 (OUT2)
SLEEP-1: R3.1, R4.1, R6.1, R12.1, R14.1, U1.3 (SLEEP), U2.3 (SLEEP), U3.3 (SLEEP), U4.3 (SLEEP)
VCC: C1.1, C2.1, C3.1, C4.1, C7.2, C8.2, C11.2, C12.2, J1.1, U1.11 (VM), U2.11 (VM), U3.11 (VM), U4.11 (VM)
VREF-1: R4.2, R5.1, U1.5 (VREF)
VREF-2: R12.2, R13.1, U2.5 (VREF)
VREF-3: R6.2, R7.1, U3.5 (VREF)
VREF-4: R14.2, R15.1, U4.5 (VREF)

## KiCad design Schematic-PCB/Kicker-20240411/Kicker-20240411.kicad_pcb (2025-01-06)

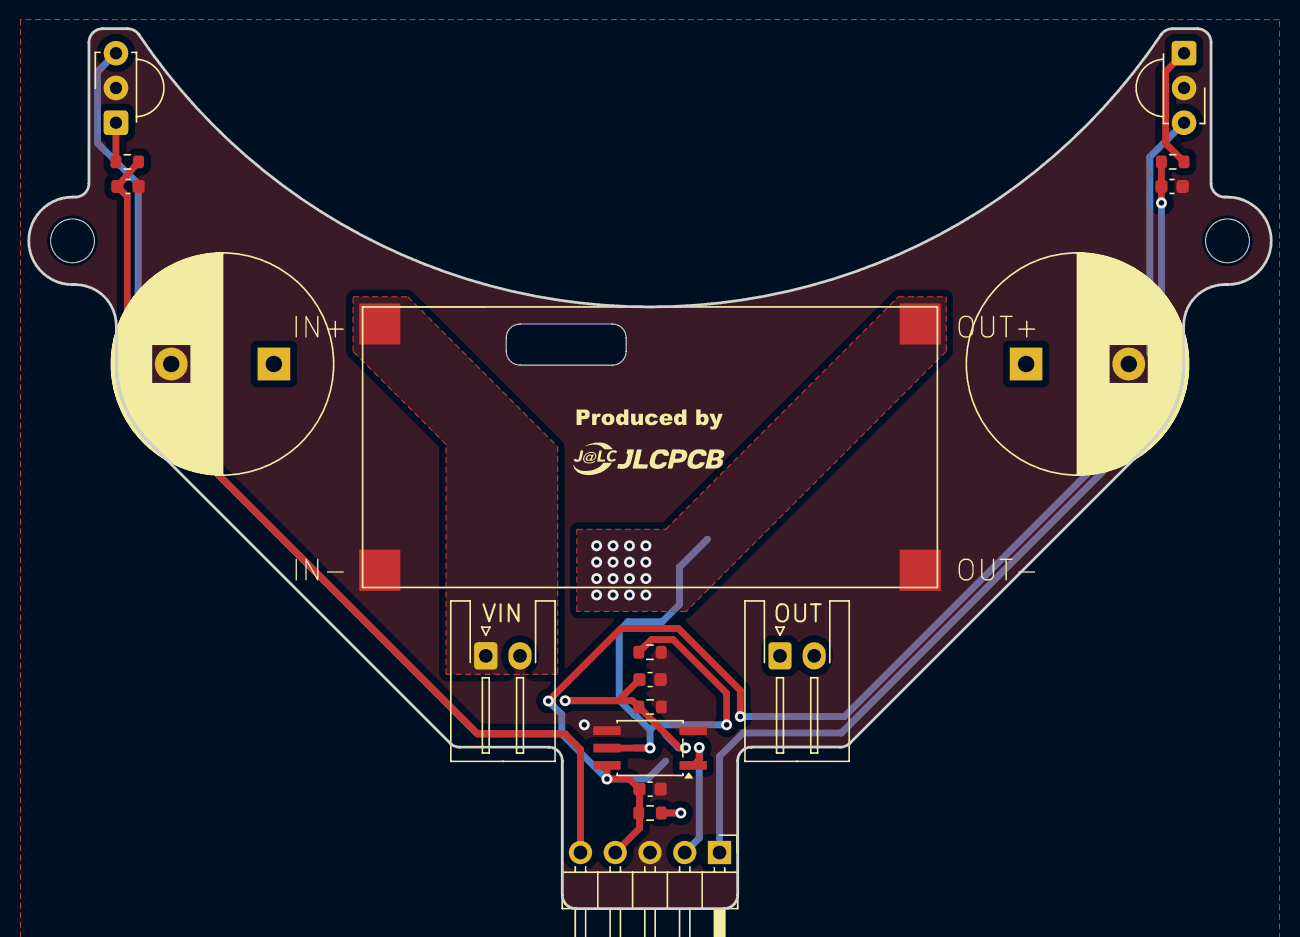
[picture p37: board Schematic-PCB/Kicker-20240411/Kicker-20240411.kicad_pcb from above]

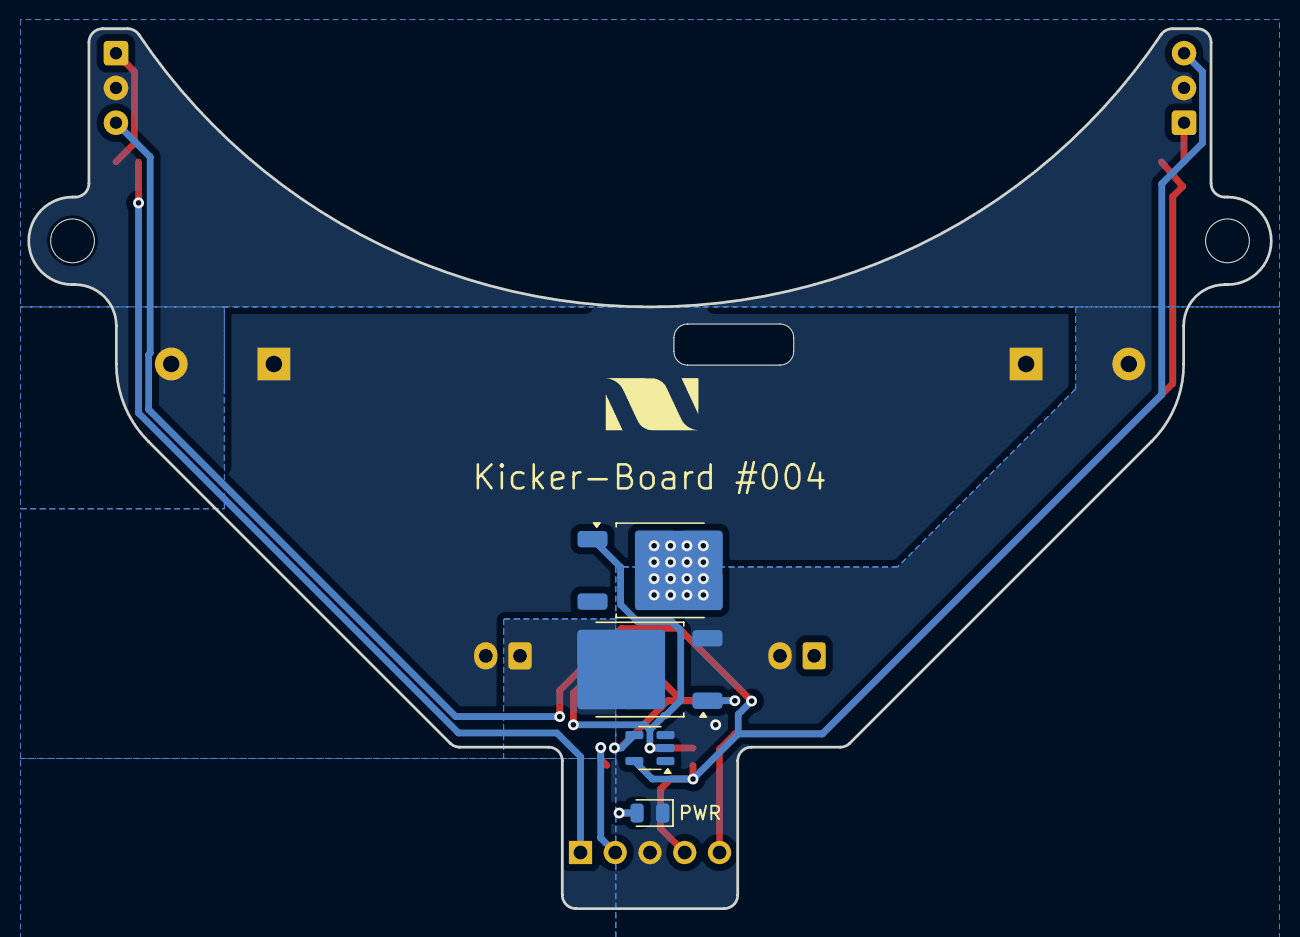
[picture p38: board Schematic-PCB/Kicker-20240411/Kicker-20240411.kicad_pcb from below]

Board: 2 copper layers, 90.8 x 64.3 mm, 22 parts (4 on the bottom side), 14 nets.

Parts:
C1, C4: 2200uF; CP_Radial_D16.0mm_P7.50mm
C2, C3: 0.33u; C_0603_1608Metric
C5, C7: 0.1uF; C_0603_1608Metric
D1: PWR; LED_0805_2012Metric
D2: SO-5_4.4x3.6mm_P1.27mm
J1, J3: Conn_01x02_Pin; JST_XH_S2B-XH-A-1_1x02_P2.50mm_Horizontal
J2: Conn_01x05_Pin; PinHeader_1x05_P2.54mm_Horizontal
Q1, Q2: NMOS; TO-252-2
R1, R2: 39K; R_0603_1608Metric
R3: 330; R_0603_1608Metric
R4, R5: 10K; R_0603_1608Metric
U1, U2: TSSP58P38; Vishay_MINICAST-3Pin
U3: XL6009-SMD
U4: SOT-23-5

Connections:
+3.3V: C5.1, D2.6 (VCC), J2.4, R3.1, U1.3 (Vs), U2.3 (Vs), U4.5 (VCC)
+48V: Q1.2 (D), U3.3 (+OUT)
GND: C1.2, C2.2, C3.2, C4.2, C5.2, C7.2, D1.1 (K), D2.3 (Cathode), D2.4 (GND), J1.2, J2.3, Q2.3 (S), R4.2, R5.2, U1.2 (GND), U2.2 (GND), U3.2 (-IN), U3.4 (-OUT), U4.3 (GND)
unnamed: D1.2 (A), R3.2
unnamed: J3.1, Q2.2 (D)
unnamed: C7.1, Q2.1 (G), R5.1, U4.4 (OUT)
unnamed: R1.1, U1.1 (OUT)
unnamed: R2.1, U2.1 (OUT)
Sig: D2.5 (VO), Q1.1 (G), R4.1, U4.2 (IN)
Sig-main: D2.1 (Anode), J2.2
VCC: J1.1, U3.1 (+IN)
VDD: C1.1, C4.1, J3.2
ball01k: C2.1, J2.1, R1.2
ball02k: C3.1, J2.5, R2.2

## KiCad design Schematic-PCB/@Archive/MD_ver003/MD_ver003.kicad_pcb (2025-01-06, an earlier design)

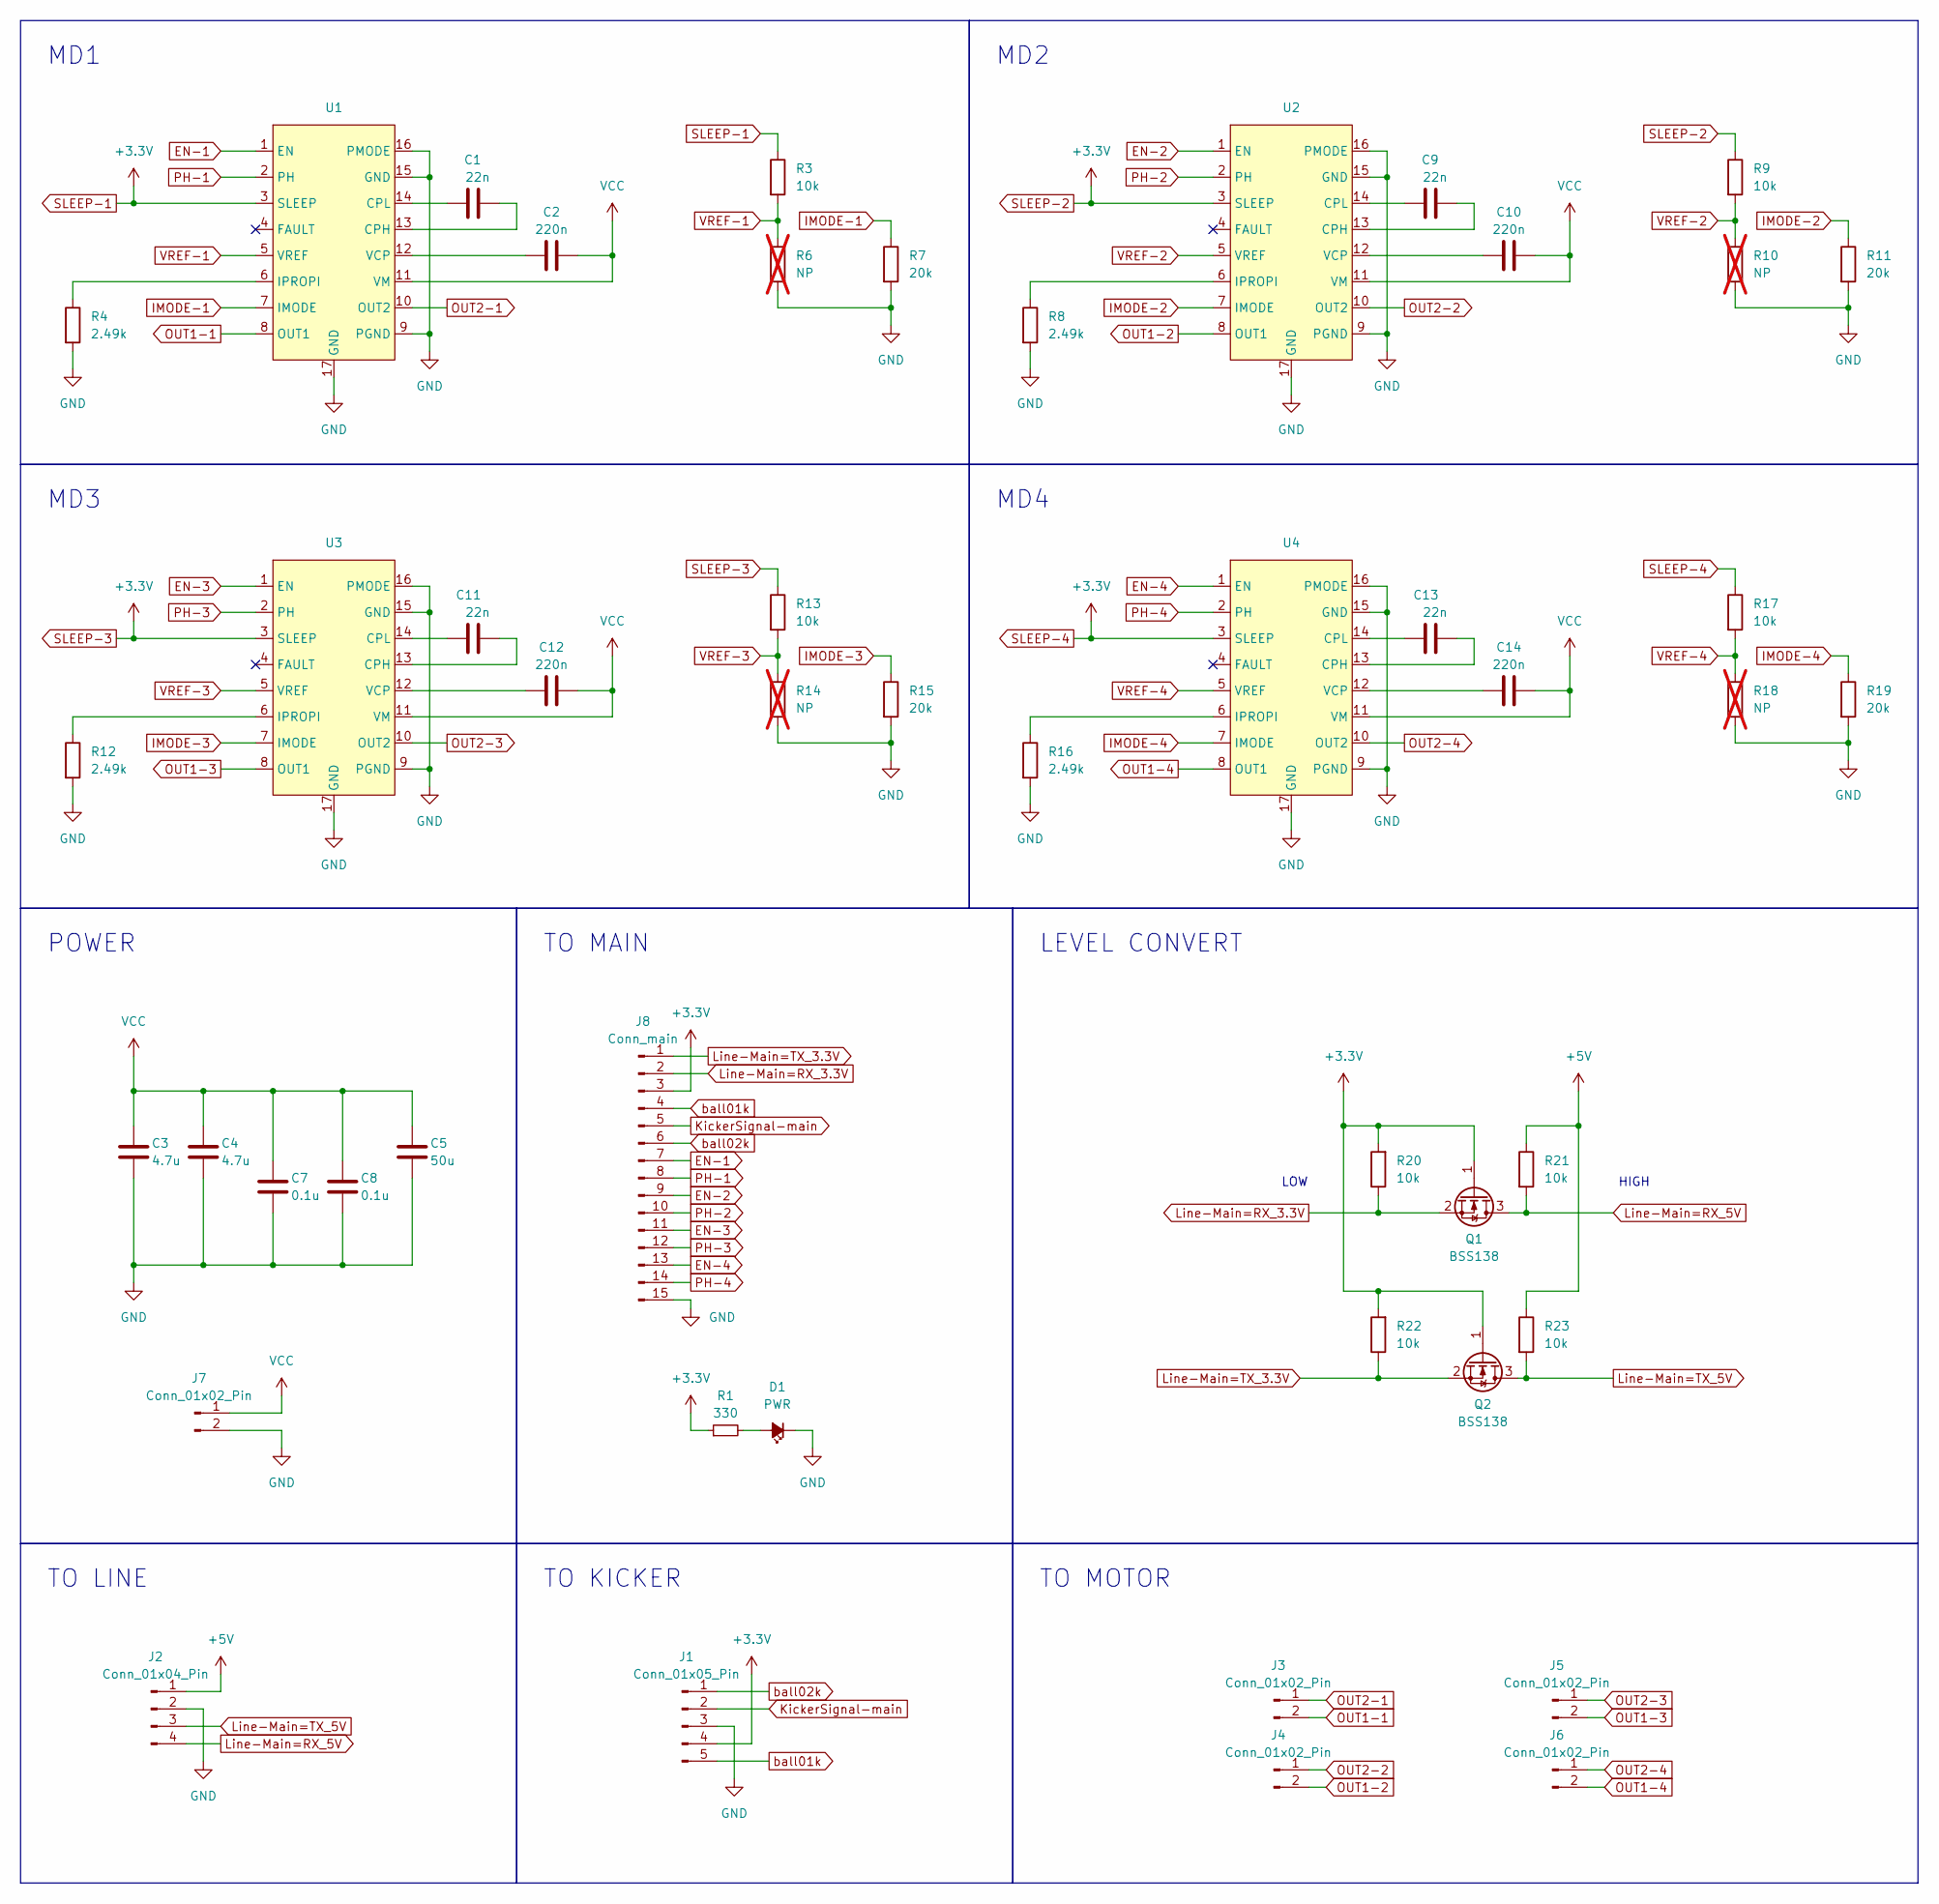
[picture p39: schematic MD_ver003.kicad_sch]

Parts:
C1, C9, C11, C13: 22n; C_0603_1608Metric
C2, C10, C12, C14: 220n; C_0603_1608Metric
C3, C4: 4.7u; C_0603_1608Metric
C5: 50u; C_0603_1608Metric
C7, C8: 0.1u; C_0603_1608Metric
D1: PWR; LED_0805_2012Metric
J1: Conn_01x05_Pin; PinSocket_1x05_P2.54mm_Horizontal
J2: Conn_01x04_Pin; JST_XH_S4B-XH-A-1_1x04_P2.50mm_Horizontal
J3, J4, J5, J6: Conn_01x02_Pin; JST_XH_B2B-XH-A_1x02_P2.50mm_Vertical
J7: Conn_01x02_Pin; XT30U-M
J8: Conn_main; TE_1-84953-5_1x15-1MP_P1.0mm_Horizontal
Q1, Q2: BSS138; SOT-23
R1: 330; R_0603_1608Metric
R3, R9, R13, R17, R20, R21, R22, R23: 10k; R_0603_1608Metric
R4, R8, R12, R16: 2.49k; R_0603_1608Metric
R6, R10, R14, R18: NP; R_0603_1608Metric; not fitted
R7, R11, R15, R19: 20k; R_0603_1608Metric
U1, U2, U3, U4: HTSSOP-16-1EP_4.4x5mm_P0.65mm_EP3.4x5mm

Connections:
+5V: J2.1, R21.1, R23.1
EN-1: J8.7, U1.1 (EN)
EN-2: J8.9, U2.1 (EN)
EN-3: J8.11, U3.1 (EN)
EN-4: J8.13, U4.1 (EN)
GND: C3.2, C4.2, C5.2, C7.2, C8.2, D1.1 (K), J1.3, J2.2, J7.2, J8.15, R4.2, R6.2, R7.2, R8.2, R10.2, R11.2, R12.2, R14.2, R15.2, R16.2, R18.2, R19.2, U1.9 (PGND), U1.15 (GND), U1.16 (PMODE), U1.17 (GND), U2.9 (PGND), U2.15 (GND), U2.16 (PMODE), U2.17 (GND), U3.9 (PGND), U3.15 (GND), U3.16 (PMODE), U3.17 (GND), U4.9 (PGND), U4.15 (GND), U4.16 (PMODE), U4.17 (GND)
IMODE-1: R7.1, U1.7 (IMODE)
IMODE-2: R11.1, U2.7 (IMODE)
IMODE-3: R15.1, U3.7 (IMODE)
IMODE-4: R19.1, U4.7 (IMODE)
KickerSignal-main: J1.2, J8.5
Line-Main=RX_3.3V: J8.2, Q1.2 (S), R20.1
Line-Main=RX_5V: J2.4, Q1.3 (D), R21.2
Line-Main=TX_3.3V: J8.1, Q2.2 (S), R22.1
Line-Main=TX_5V: J2.3, Q2.3 (D), R23.2
unnamed: D1.2 (A), R1.2
unnamed: C1.2, U1.13 (CPH)
unnamed: C1.1, U1.14 (CPL)
unnamed: R4.1, U1.6 (IPROPI)
unnamed: C2.1, U1.12 (VCP)
unnamed: C9.2, U2.13 (CPH)
unnamed: C9.1, U2.14 (CPL)
unnamed: R8.1, U2.6 (IPROPI)
unnamed: C10.1, U2.12 (VCP)
unnamed: C11.2, U3.13 (CPH)
unnamed: C11.1, U3.14 (CPL)
unnamed: R12.1, U3.6 (IPROPI)
unnamed: C12.1, U3.12 (VCP)
unnamed: C13.2, U4.13 (CPH)
unnamed: C13.1, U4.14 (CPL)
unnamed: R16.1, U4.6 (IPROPI)
unnamed: C14.1, U4.12 (VCP)
OUT1-1: J3.2, U1.8 (OUT1)
OUT1-2: J4.2, U2.8 (OUT1)
OUT1-3: J5.2, U3.8 (OUT1)
OUT1-4: J6.2, U4.8 (OUT1)
OUT2-1: J3.1, U1.10 (OUT2)
OUT2-2: J4.1, U2.10 (OUT2)
OUT2-3: J5.1, U3.10 (OUT2)
OUT2-4: J6.1, U4.10 (OUT2)
PH-1: J8.8, U1.2 (PH)
PH-2: J8.10, U2.2 (PH)
PH-3: J8.12, U3.2 (PH)
PH-4: J8.14, U4.2 (PH)
SLEEP-1: J1.4, J8.3, Q1.1 (G), Q2.1 (G), R1.1, R3.1, R9.1, R13.1, R17.1, R20.2, R22.2, U1.3 (SLEEP), U2.3 (SLEEP), U3.3 (SLEEP), U4.3 (SLEEP)
VCC: C2.2, C3.1, C4.1, C5.1, C7.1, C8.1, C10.2, C12.2, C14.2, J7.1, U1.11 (VM), U2.11 (VM), U3.11 (VM), U4.11 (VM)
VREF-1: R3.2, R6.1, U1.5 (VREF)
VREF-2: R9.2, R10.1, U2.5 (VREF)
VREF-3: R13.2, R14.1, U3.5 (VREF)
VREF-4: R17.2, R18.1, U4.5 (VREF)
ball01k: J1.5, J8.4
ball02k: J1.1, J8.6

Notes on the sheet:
MD3
LEVEL CONVERT
HIGH
TO MOTOR
TO LINE
TO KICKER
POWER
MD2
MD4
LOW
TO MAIN
MD1

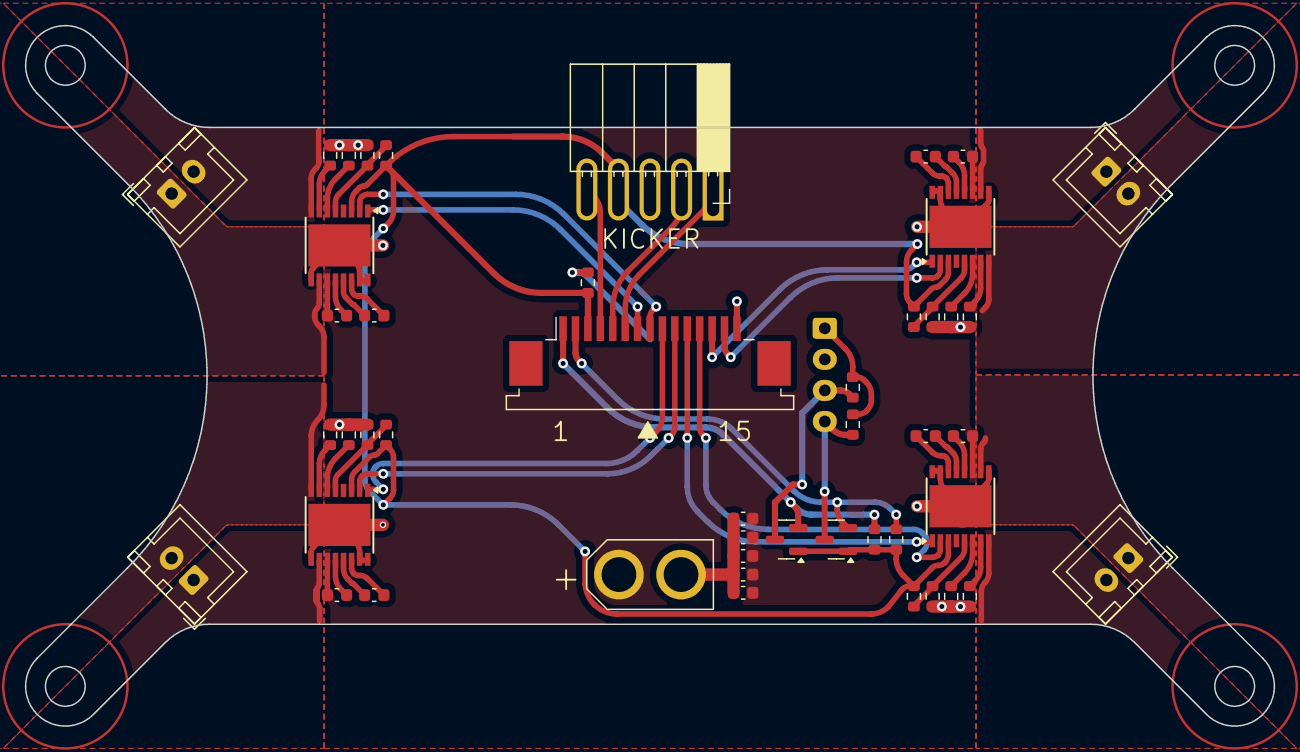
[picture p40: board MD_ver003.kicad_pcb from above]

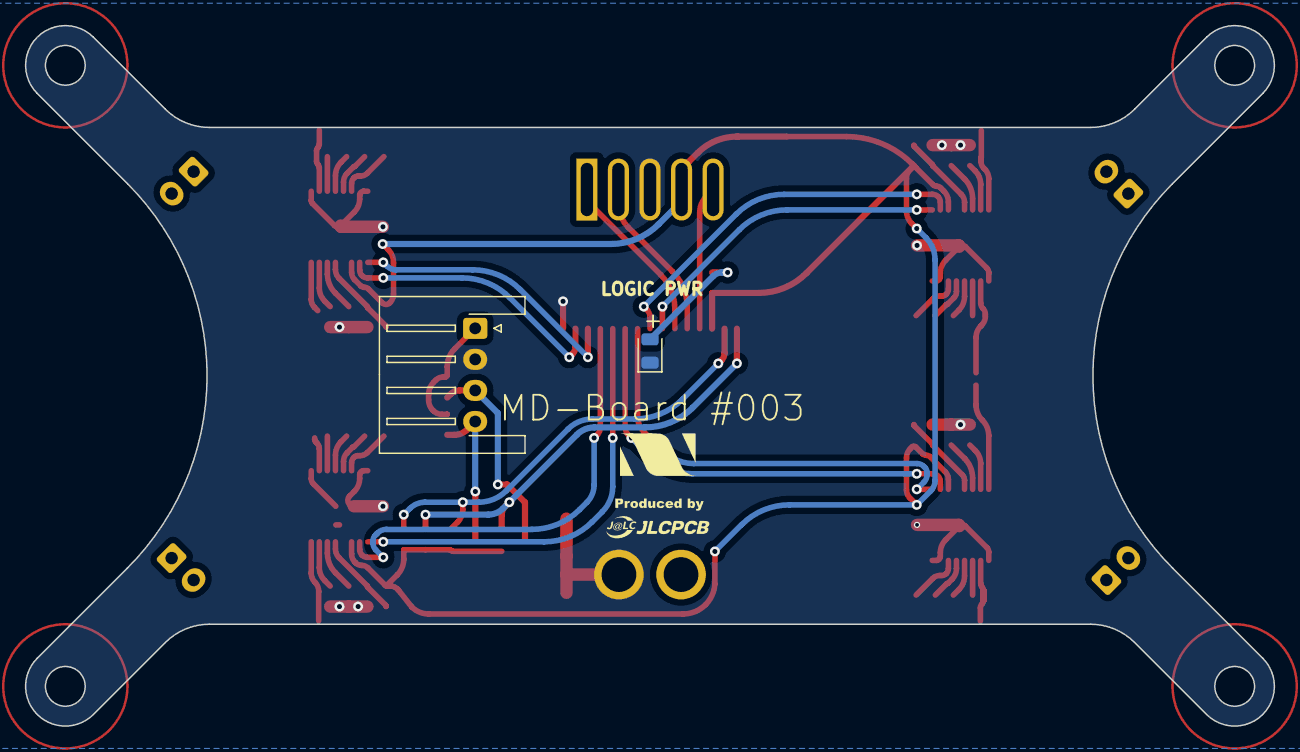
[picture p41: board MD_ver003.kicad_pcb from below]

Board: 2 copper layers, 100.5 x 56.4 mm, 49 parts (2 on the bottom side), 52 nets.

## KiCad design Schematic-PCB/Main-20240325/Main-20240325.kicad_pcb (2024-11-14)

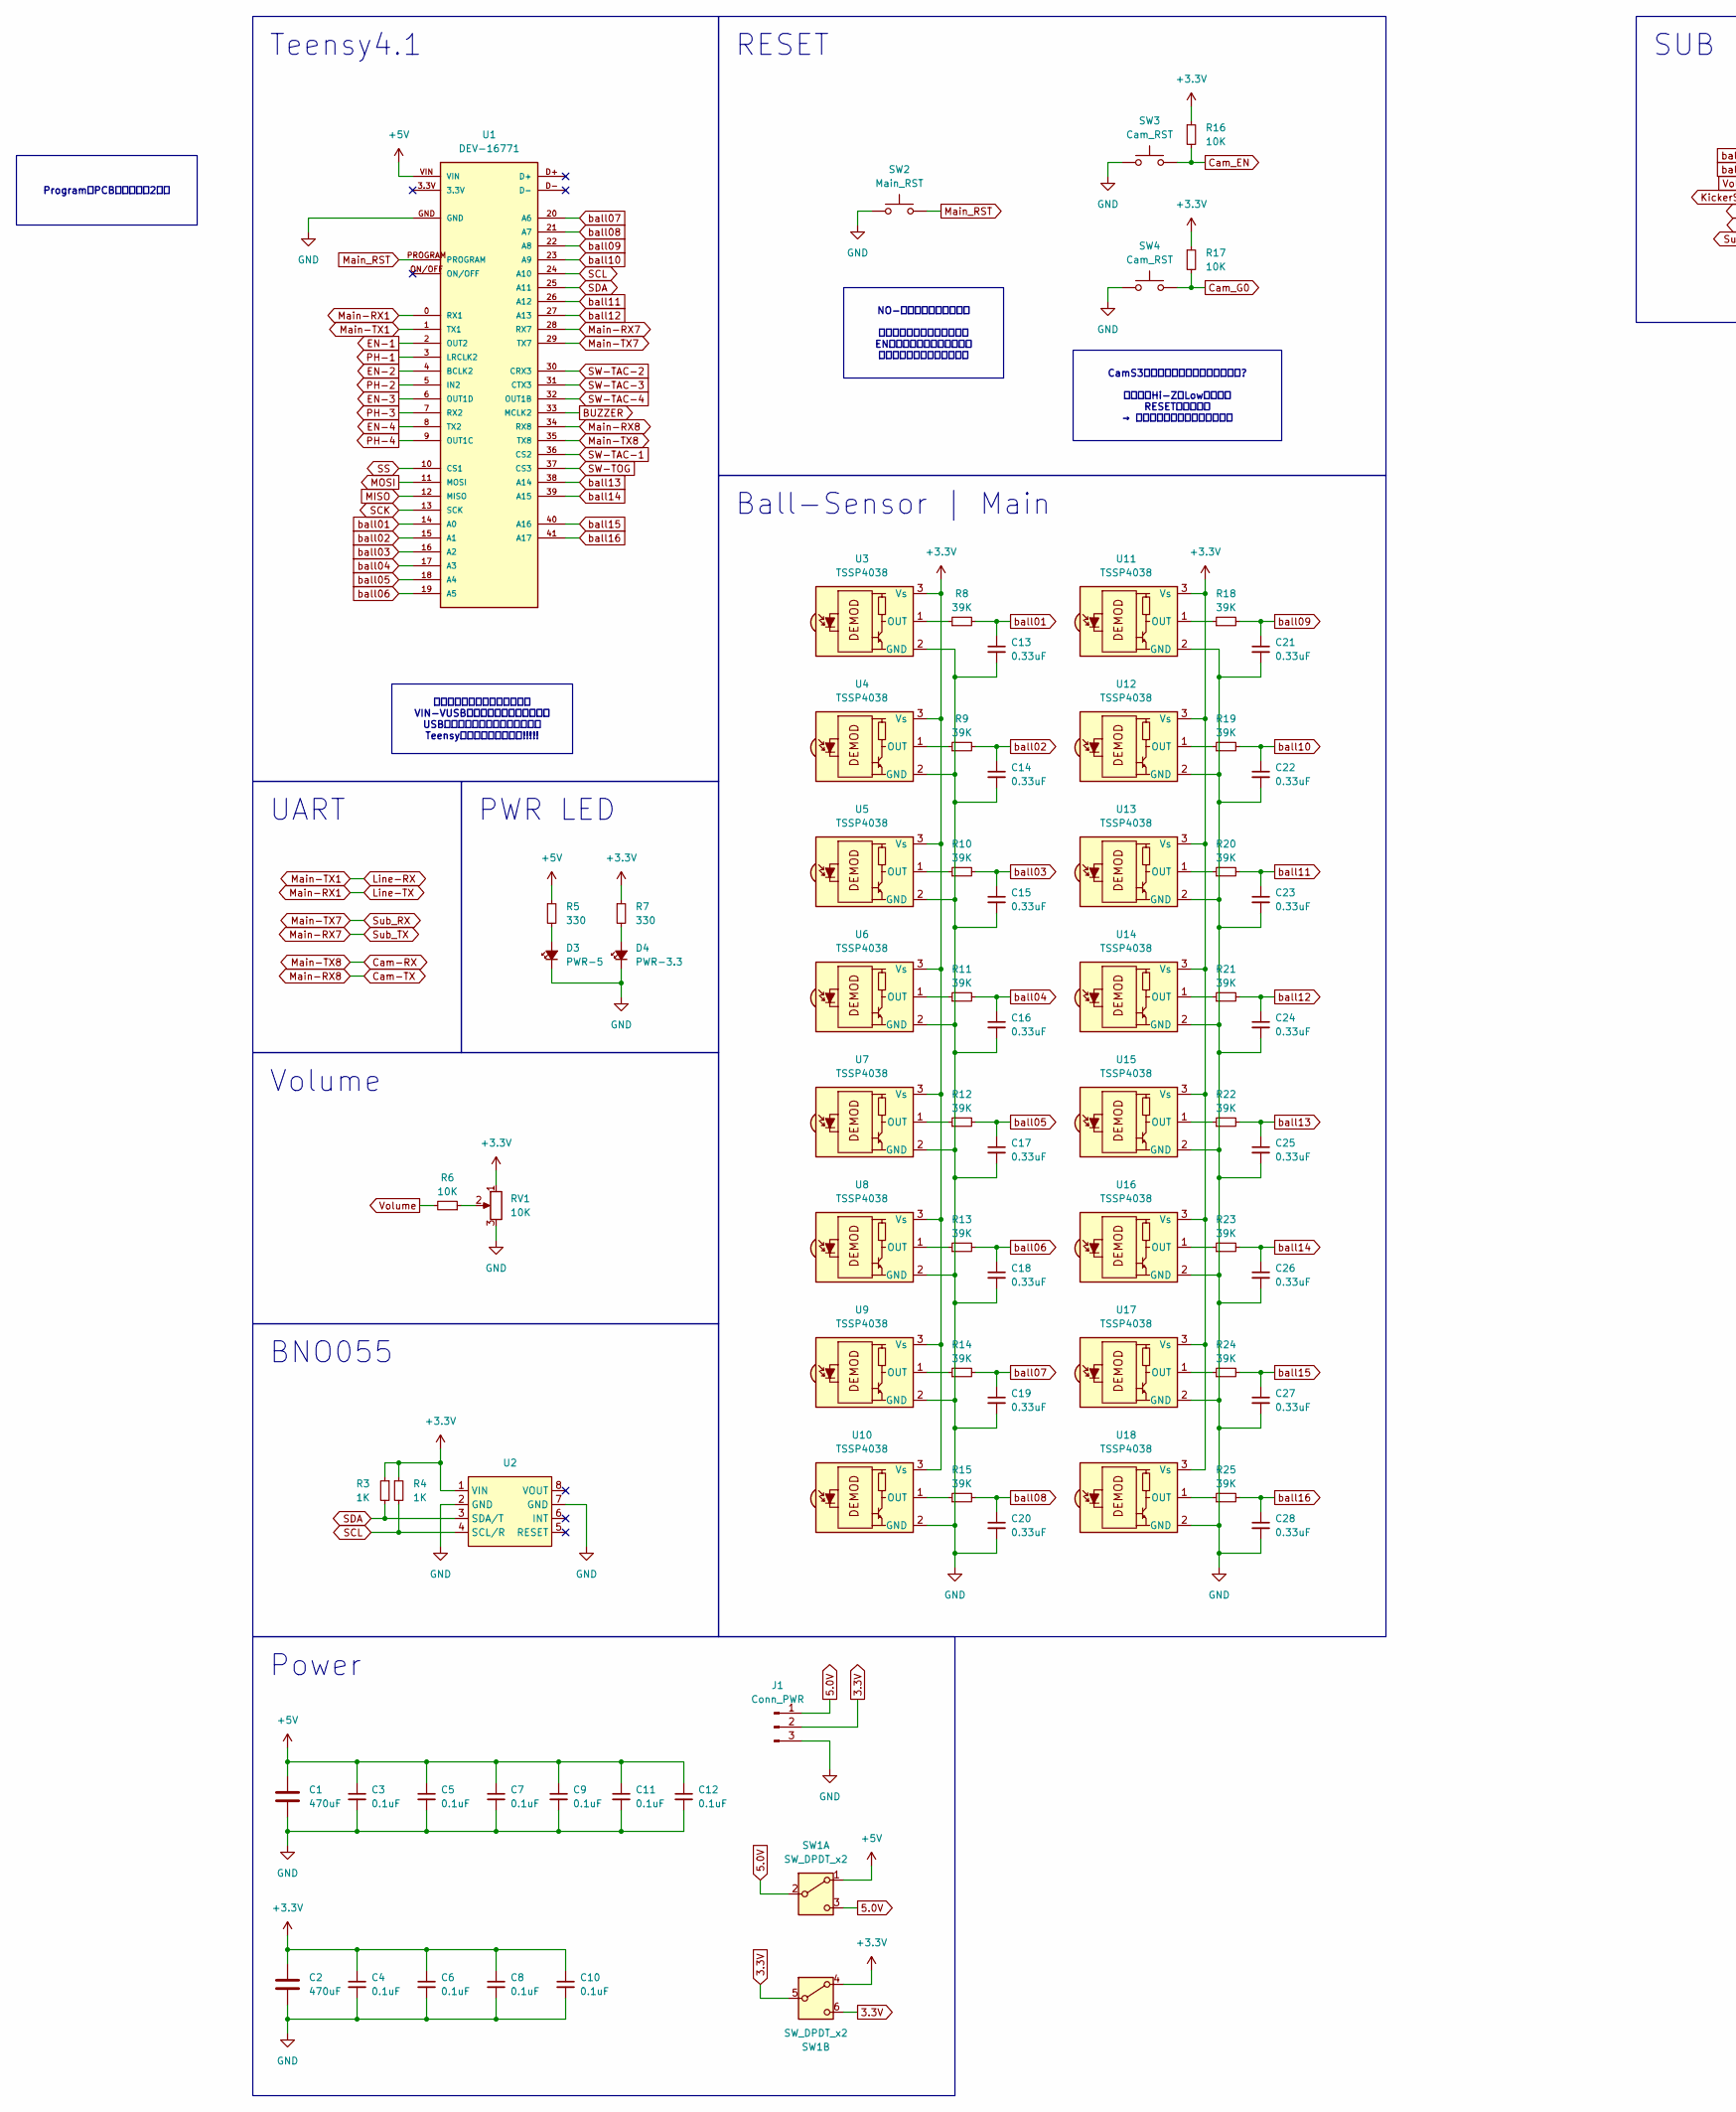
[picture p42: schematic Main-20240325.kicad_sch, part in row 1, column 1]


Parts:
C1, C2: 470uF; CP_Radial_D8.0mm_P3.50mm
C3, C4, C5, C6, C7, C8, C9, C10, C11, C12: 0.1uF; C_0603_1608Metric
C13, C14, C15, C16, C17, C18, C19, C20, C21, C22, C23, C24, C25, C26, C27, C28: 0.33uF; C_0603_1608Metric
D3: PWR-5; LED_0603_1608Metric
D4: PWR-3.3; LED_0603_1608Metric
D5: D_Small; D_A-405_P7.62mm_Horizontal
J1: Conn_PWR; JST_XH_B3B-XH-A_1x03_P2.50mm_Vertical
J2: CamS3-6; PinSocket_1x06_P2.54mm_Vertical
J3: CamS3-4; NS-Tech_Grove_1x04_P2mm_Vertical
J4: Pixy 2.1; IDC-Header_2x05_P2.54mm_Vertical
J5: Conn_MD; 1.0K-FX-15PWB
J6: Conn_Dribbler; JST_XH_B4B-XH-A_1x04_P2.50mm_Vertical
J7: Conn_UI; JST_XH_B10B-XH-A_1x10_P2.50mm_Vertical
J8, J9, J10: Conn_NeoPixel; Connector
R3, R4: 1K; R_0603_1608Metric
R5, R7: 330; R_0603_1608Metric
R6, R16, R17: 10K; R_0603_1608Metric
R8, R9, R10, R11, R12, R13, R14, R15, R18, R19, R20, R21, R22, R23, R24, R25: 39K; R_0603_1608Metric
RV1: 10K; 3362P
SW1: SW_DPDT_x2; 2MD1-T2-B4-M2-Q-N
SW2: Main_RST; TVBP06-B043C
SW3, SW4: Cam_RST; TVBP06-B043C
U1: DEV-16771; MODULE_DEV-16771
U2: BNO055
U3, U4, U5, U6, U7, U8, U9, U10, U11, U12, U13, U14, U15, U16, U17, U18: TSSP4038
U19: XIAO ESP32C3

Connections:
3.3V: J1.2, SW1.5 (B), SW1.6 (C)
5.0V: J1.1, SW1.2 (B), SW1.3 (C)
+3.3V: C2.1, C4.1, C6.1, C8.1, C10.1, J5.13, J6.3, J7.1, R3.1, R4.1, R7.1, R16.1, R17.1, RV1.1, SW1.4 (A), U2.1 (VIN), U3.3 (Vs), U4.3 (Vs), U5.3 (Vs), U6.3 (Vs), U7.3 (Vs), U8.3 (Vs), U9.3 (Vs), U10.3 (Vs), U11.3 (Vs), U12.3 (Vs), U13.3 (Vs), U14.3 (Vs), U15.3 (Vs), U16.3 (Vs), U17.3 (Vs), U18.3 (Vs)
+5V: C1.1, C3.1, C5.1, C7.1, C9.1, C11.1, C12.1, D5.2 (A), J2.1, J3.3, J4.2, J8.1, J8.2, J9.1, J9.2, J10.1, J10.2, R5.1, SW1.1 (A), U1.VIN
BUZZER: J7.10, U1.33 (MCLK2)
Cam-RX: J2.3, J3.2, U1.35 (TX8)
Cam-TX: J2.2, J3.1, U1.34 (RX8)
Cam_EN: J2.4, R16.2, SW3.2
Cam_G0: J2.5, R17.2, SW4.2
EN-1: J5.2, U1.2 (OUT2)
EN-2: J5.4, U1.4 (BCLK2)
EN-3: J5.6, U1.6 (OUT1D)
EN-4: J5.8, U1.8 (TX2)
EN-D: J6.2, U19.6 (SCL_D5)
GND: C1.2, C2.2, C3.2, C4.2, C5.2, C6.2, C7.2, C8.2, C9.2, C10.2, C11.2, C12.2, C13.2, C14.2, C15.2, C16.2, C17.2, C18.2, C19.2, C20.2, C21.2, C22.2, C23.2, C24.2, C25.2, C26.2, C27.2, C28.2, D3.1 (K), D4.1 (K), J1.3, J2.6, J3.4, J4.6, J5.1, J6.4, J7.2, J8.4, J8.5, J9.3, J9.4, J9.5, J10.3, J10.4, J10.5, RV1.3, SW2.1, SW3.1, SW4.1, U1.GND, U2.2 (GND), U2.7 (GND), U3.2 (GND), U4.2 (GND), U5.2 (GND), U6.2 (GND), U7.2 (GND), U8.2 (GND), U9.2 (GND), U10.2 (GND), U11.2 (GND), U12.2 (GND), U13.2 (GND), U14.2 (GND), U15.2 (GND), U16.2 (GND), U17.2 (GND), U18.2 (GND), U19.13 (GND)
KickerSignal: J5.11, U19.4 (A3_D3)
Line-RX: J5.15, U1.1 (TX1)
Line-TX: J5.14, U1.0 (RX1)
MISO: J4.1, U1.12 (MISO)
MOSI: J4.4, U1.11 (MOSI)
Main-RX7: U1.28 (RX7), U19.7 (TX_D6)
Main-TX7: U1.29 (TX7), U19.8 (RX_D7)
Main_RST: SW2.2, U1.PROGRAM
NeoPixel_PWM: J8.3, U19.11 (MOSI_D10)
unnamed: D3.2 (A), R5.2
unnamed: D4.2 (A), R7.2
unnamed: D5.1 (K), U19.14 (5V)
unnamed: R6.1, RV1.2
unnamed: R8.1, U3.1 (OUT)
unnamed: R9.1, U4.1 (OUT)
unnamed: R10.1, U5.1 (OUT)
unnamed: R11.1, U6.1 (OUT)
unnamed: R12.1, U7.1 (OUT)
unnamed: R13.1, U8.1 (OUT)
unnamed: R14.1, U9.1 (OUT)
unnamed: R15.1, U10.1 (OUT)
unnamed: R18.1, U11.1 (OUT)
unnamed: R19.1, U12.1 (OUT)
unnamed: R20.1, U13.1 (OUT)
unnamed: R21.1, U14.1 (OUT)
unnamed: R22.1, U15.1 (OUT)
unnamed: R23.1, U16.1 (OUT)
unnamed: R24.1, U17.1 (OUT)
unnamed: R25.1, U18.1 (OUT)
PH-1: J5.3, U1.3 (LRCLK2)
PH-2: J5.5, U1.5 (IN2)
PH-3: J5.7, U1.7 (RX2)
PH-4: J5.9, U1.9 (OUT1C)
PH-D: J6.1, U19.5 (SDA_D4)
SCK: J4.3, U1.13 (SCK)
SCL: J7.9, R4.2, U1.24 (A10), U2.4 (SCL/R)
SDA: J7.8, R3.2, U1.25 (A11), U2.3 (SDA/T)
SS: J4.7, U1.10 (CS1)
SW-TAC-1: J7.4, U1.36 (CS2)
SW-TAC-2: J7.5, U1.30 (CRX3)
SW-TAC-3: J7.6, U1.31 (CTX3)
SW-TAC-4: J7.7, U1.32 (OUT1B)
SW-TOG: J7.3, U1.37 (CS3)
Volume: R6.2, U19.3 (A2_D2)
ball01: C13.1, R8.2, U1.14 (A0)
ball01k: J5.10, U19.1 (A0_D0)
ball02: C14.1, R9.2, U1.15 (A1)
ball02k: J5.12, U19.2 (A1_D1)
ball03: C15.1, R10.2, U1.16 (A2)
ball04: C16.1, R11.2, U1.17 (A3)
ball05: C17.1, R12.2, U1.18 (A4)
ball06: C18.1, R13.2, U1.19 (A5)
ball07: C19.1, R14.2, U1.20 (A6)
ball08: C20.1, R15.2, U1.21 (A7)
ball09: C21.1, R18.2, U1.22 (A8)
ball10: C22.1, R19.2, U1.23 (A9)
ball11: C23.1, R20.2, U1.26 (A12)
ball12: C24.1, R21.2, U1.27 (A13)
ball13: C25.1, R22.2, U1.38 (A14)
ball14: C26.1, R23.2, U1.39 (A15)
ball15: C27.1, R24.2, U1.40 (A16)
ball16: C28.1, R25.2, U1.41 (A17)

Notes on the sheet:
UI ドリブラー MD NeoPixel への ピンアサインは 確認済み 2024.11.02 18.38
Ball-Sensor | Main
RESET
To CamS3 Grove
To NeoPixel2
BNO055
Teensy4.1
To NeoPixel3
SUB
To MD
To Dribbler
To NeoPixel1
To UI
[Serial-Communications] Teensy4.1-ESP32: X SPI O UART X I2C Teensy4.1-ATmega2560: X SPI O UART X I2C Teensy4.1-BNO055: X SPI X UART O I2C Teensy4.1-Pixy2.1: O SPI X UART X I2C Teensy4.1-UnitCamS3: X SPI O UART X I2C
CamS3に関してはプルアップ必要カモ? おそらくHi-ZとLowの違いで RESETかけている → 誤動作防止用に抵抗付しておく
To Pixy2.1
To CamS3
NO-プルアップで確認済み 元のモジュール化基板にある ENボタンにもプルアップ抵抗 は確認できなかったためなし
Power
UART
使用前には必ず開発ボード裏の VIN-VUSBジャンパをカットすること USBケーブルとの電源の混合が起き Teensyが燃えるため絶対に!!!!!
ProgramのPCBの足の数を2本に
Volume
PWR LED



Board: 4 copper layers, 112.0 x 112.0 mm, 88 parts (70 on the bottom side), 77 nets.

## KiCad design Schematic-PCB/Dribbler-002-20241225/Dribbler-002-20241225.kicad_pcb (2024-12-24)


Board: 2 copper layers, 32.3 x 27.8 mm, 8 parts (0 on the bottom side), 9 nets.

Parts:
J3: Conn_01x02_Pin; JST_XH_S2B-XH-A-1_1x02_P2.50mm_Horizontal
LGC: Signal; LED_0805_2012Metric
PWR: Power; LED_0805_2012Metric
R1, R2: 330; R_0603_1608Metric
SIG/LOGIC: Conn_01x04_Pin; JST_XH_B4B-XH-A_1x04_P2.50mm_Vertical
U1: DRV8874 module
VIN: Conn_01x02_Pin; JST_XH_S2B-XH-A-1_1x02_P2.50mm_Horizontal

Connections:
+3.3V: R1.2, SIG/LOGIC.3, U1.6 (SLEEP)
EN: SIG/LOGIC.2, U1.3 (EN)
GND: LGC.1 (K), PWR.1 (K), SIG/LOGIC.4, U1.2 (GND), U1.5 (PMODE), U1.13 (GND), VIN.2
unnamed: LGC.2 (A), R1.1
unnamed: PWR.2 (A), R2.1
OUT1: J3.1, U1.12 (OUT1)
OUT2: J3.2, U1.11 (OUT2)
PH: SIG/LOGIC.1, U1.4 (PH)
VCC: R2.2, U1.1 (VM), VIN.1

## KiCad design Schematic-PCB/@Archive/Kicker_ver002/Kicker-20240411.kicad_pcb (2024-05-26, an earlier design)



Board: 2 copper layers, 90.8 x 52.5 mm, 21 parts (13 on the bottom side), 14 nets.

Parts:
C2: 0.1uF; C_0603_1608Metric
C3, C4: 2200uF; CP_Radial_D16.0mm_P7.50mm
C5, C6: 0.33u; C_0603_1608Metric
D2: SO-5_4.4x3.6mm_P1.27mm
D3: PWR; LED_0805_2012Metric
DIRECT: Jumper_2_Small_Open; SolderJumper-2_P1.3mm_Open_Pad1.0x1.5mm
KI.: Conn_01x02_Pin; JST_XH_S2B-XH-A-1_1x02_P2.50mm_Horizontal
MD: Conn_01x05_Pin; JST_XH_S5B-XH-A-1_1x05_P2.50mm_Horizontal
Q1: NMOS; TO-252-2
R1: 10K; R_0603_1608Metric
R2: 330; R_0603_1608Metric
R3, R4: 39K; R_0603_1608Metric
U1: XL6009-SMD
U2: 74LVC1G04; SOT-23-5
U3, U4: TSSP58P38; Vishay_MINICAST-3Pin
VIN: Conn_01x02_Pin; JST_XH_S2B-XH-A-1_1x02_P2.50mm_Horizontal
W/NOT: Jumper_2_Small_Open; SolderJumper-2_P1.3mm_Open_Pad1.0x1.5mm

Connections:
+3.3V: C2.1, D2.6 (VCC), MD.4, R2.1, U2.5 (VCC), U3.3 (Vs), U4.3 (Vs)
GND: C2.2, C3.2, C4.2, C5.2, C6.2, D2.3 (Cathode), D2.4 (GND), D3.1 (K), MD.3, Q1.3 (S), R1.2, U1.2 (-IN), U1.4 (-OUT), U2.3 (GND), U3.2 (GND), U4.2 (GND), VIN.2
KickerPower: C3.1, C4.1, KI..1, U1.3 (+OUT)
KickerSignal: D2.5 (VO), DIRECT.1 (A), U2.2
KickerSignal-main: D2.1 (Anode), MD.2
unnamed: D3.2 (A), R2.2
unnamed: KI..2, Q1.2 (D)
unnamed: DIRECT.2 (B), Q1.1 (G), R1.1, W/NOT.2 (B)
unnamed: U2.4, W/NOT.1 (A)
unnamed: R3.1, U3.1 (OUT)
unnamed: R4.1, U4.1 (OUT)
VCC: U1.1 (+IN), VIN.1
ball01k: C5.1, MD.5, R3.2
ball02k: C6.1, MD.1, R4.2

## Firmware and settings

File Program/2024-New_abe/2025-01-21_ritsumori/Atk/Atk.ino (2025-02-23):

// new atacker ritsumori
// Teensy4.1
// 2024-02-23

#include <cmath>

#include <Wire.h>

#include "Ball.hpp"
#include "Camera.hpp"
#include "Dir.hpp"
#include "Display.hpp"
#include "Line.hpp"
#include "Motor.hpp"
#include "Sub.hpp"
#include "UI.hpp"

Ball ball;
Camera camera;
Dir dir;
Display display;
Line line;
Motor motor;
Sub sub;
UI ui;

// #include "Kicker.hpp"
// Kicker kicker;

using namespace std;



bool is_display_on = true;

// 周り込み
float h = 20;         // ヒステリシス
float r = 11600.0;    // 回り込みの半径
float p_gain = 1.5;
float d_gain = 3.0;  // Test

float offset = 1.0;


// ステートマシン
State state      = State::KickOff;
State state_prev = State::KickOff;
uint32_t state_begin = 0;



void setup() {
  Serial.begin(115200);
  Serial.println("2024-12-24 TOINIOT2 kansai");

  ball.begin();
  camera.begin();
  display.begin();
  dir.begin();
  line.begin(115200);
  motor.begin();
  sub.begin();
  ui.begin();

  // calibration
  uint8_t system=0, gyro=0, accel=0, mag=0;
  while(system<3 || gyro<3 || mag<3){
    display.printd(8,8,to_string(COMPILE));

    dir.calibration(&system, &gyro, &accel, &mag);
    digitalWrite(LED_BUILTIN, HIGH);

    display.printd(32,16,"system: "+to_string(system));
    display.printd(32,24,"gyro  : "+to_string(gyro));
    display.printd(32,32,"accel : "+to_string(accel));
    display.printd(32,40,"mag   : "+to_string(mag));

    display.printd(120, 8, "skip", ALIGN::RIGHT);
    ui.read();
    if(ui.buttonUp(1)) break;

    display.draw();
  }

  // 攻め方向が設定されるまで待機
  display.printd(8,56,"set dir");
  display.draw();
  while(!ui.buttonUp(0)){ ui.read(); }
  display.draw();

  dir.setDefault();

  Serial.println("start");
}



void loop() {
  // delayなしで約3(ms)

  ball.read();
  camera.read();
  dir.read();
  line.read();
  sub.read();
  ui.read();

static float _push_move = 2.0, _push_dir = 5.0;
  float push_move = (int)(_push_move * 10.0f), push_dir = (int)(_push_dir * 10.0f);

  // ディスプレイ
  if(ui.is_toggle){
    Serial.println("display");
    camera.lock = false;
    if(ui.buttonUp(0)) display.next();

    display.addValiables("p_gain :"+to_string(p_gain), &p_gain);
    display.addValiables("d_gain :"+to_string(d_gain), &d_gain);
    // display.addValiables("offset: "+to_string(offset), &offset);
    // display.addValiables("x: "+to_string(dir.x), &dir.x);
    // display.addValiables("y: "+to_string(dir.y), &dir.y);
    // display.addValiables("z: "+to_string(dir.z), &dir.z);
    // display.addValiables("accel_avr: "+to_string(dir.accel_avr), &dir.accel_avr);
    // display.addValiables("move: "+to_string(push_move), &_push_move);
    // display.addValiables("dir : "+to_string(push_dir), &_push_dir);

    display.debug();
    display.draw();
    is_display_on = true;

    state = State::KickOff;
    // state = State::Follow;
    // state = State::Test;
    // state = State::Pushing;
    state_begin = millis();

    motor.set(0,0,0,0);

    motor.avr();
    motor.write();
    delay(10);


    return;
  }
  // ディスプレイを消灯
  if(is_display_on){
    display.draw();
    is_display_on = false;
  }


  // ステートマシンを更新
  if(state != state_prev){
    state_begin = millis();
  }
  state_prev = state;
  uint32_t state_elapsed = millis() - state_begin;
  int line_flag = 0;



  // ok: キックオフ
  if(state == State::KickOff){
    if(line.on) line_flag = 2;
    motor.moveDirFast(ball.dir, 100);
    motor.setDirAdd(dir.dir, dir.dir_prev, dir.p_gain, dir.d_gain);


    // 後ろ向き -> 故障復帰
    if(abs(dir.dir) > 90){
      state = State::Damaged;
    }

    // 保持 -> ドリブル
    if(ball.is_hold){
      state = State::Dribble;
    }

    // 0.5秒経過 -> 回り込み
    if(state_elapsed > 500){
      state = State::Follow;
    }

  }



  // ok: 故障復帰
  else if(state == State::Damaged){
    motor.setDir(dir.dir, dir.dir_prev, dir.p_gain, dir.d_gain);
    if(line.on) line_flag = 1;


    // 45度以内 -> 回り込み
    if(abs(dir.dir) < 45){
      state = State::Follow;
    }
  }



  // ToDo: 回り込み
  static int dir_type = 0;  // ゴールに向けるやつ ドリブルの判定でも使うためココに配置
  if(state == State::Follow){
    float move_dir = 0;
    bool face_flag = true;

    // 直進

    // PD
    if(abs(ball.dir)<h){
      move_dir = ball.dir * p_gain - d_gain*(ball.dir - ball.dir_prev);
      // move_dir = ball.dir * p_gain;
      h = 45;
      face_flag = false;
    }
    // 円周上
    else if(ball.distance < r){
      float theta = 90 + (r-ball.distance) * 90 / r;
      move_dir = ball.dir + (ball.dir>0?theta:-theta);
      h = 30;
      // face_flag = false;
    }
    //接線
    else{
      float theta = degrees(asin(r / ball.distance));
      move_dir = ball.dir + (ball.dir>0?theta:-theta);
      h = 30;
    }
    motor.moveDir(move_dir, 75);

    // 白線処理
    if(line.on) line_flag = 1;


    // ゴールに向ける
    static float  face = 0;
    static uint32_t t_begin = 0;

    if(face_flag){
      switch(dir_type){
        case 0:
          face = 0;

          // ゴールに近い場合のみ
          if(camera.atk.h > 24 && millis()-t_begin > 500){
          // if(camera.atk.h > 23){
            if(camera.atk.dir < -16){
            // if(camera.atk.x1 > 160){
              dir_type = 1;
              face = 20;
              t_begin = millis();
            }else if(camera.atk.dir > 16){
            // }else if(camera.atk.x1 < 245){
              dir_type = 2;
              face = -20;
              t_begin = millis();
            }
          }
          break;
        // ロボットを左に向ける
        case 1:
          face = 20;
          if(camera.atk.dir > 18 && millis()-t_begin > 0){
          // if(camera.atk.x2 < 170){
            dir_type = 0;
            t_begin = millis();
          }
          break;
        // ロボットを右に向ける
        case 2:
          face = -20;
          if(camera.atk.dir < -18 && millis()-t_begin > 0){
          // if(camera.atk.x1 > 170){
            dir_type = 0;
            t_begin = millis();
          }
          break;
      }
    }
    // motor.setDirAdd(dir.dir + face, dir.dir_prev, dir.p_gain, dir.d_gain);
    motor.setDirAdd(dir.dir, dir.dir_prev, dir.p_gain, dir.d_gain);


    // ボールを保持 -> ゴールに向かう
    if(ball.is_hold){
      // Test
      state = State::Dribble;
      state_elapsed = 0;
    }

    // 押し込み
    if(state_elapsed > 4000 && abs(dir.dir) < 15 && camera.atk.is_visible && camera.atk.h > 50 && abs(ball.dir) < 25 && abs(line.dir) < 5){
      line_flag = 0;
      state = State::Oshikomi;
    }

    if(!ball.is_exist) state = State::NoBall;

  }



  // ToDo: ゴールに向かう
  static uint32_t dribble_end = millis(); // ドリブルの終了時間(差分を計算して白線避けに使用する)
  if(state == State::Dribble){
    // ボールを持ち始めたときのゴールまでの距離で方式を決定
    static bool is_decided = false;
    static int  type = 0;

    if(!is_decided){
      // ゴールに近すぎる場合、平行移動ですら躱せないためねじる
      if((camera.atk.h > 38 && !camera.is_center) || (abs(camera.chance_dir) > 20 && camera.atk.h > 36)){
      // if(camera.atk.h > 36){
        type = 0;
      }
      // ゴールに近い場合、姿勢制御が間に合わないため平行移動
      else if(camera.atk.h > 34){
        type = 1;
      }
      // 間に合う場合、ゴールに向けて姿勢制御しながら攻める
      else{
        type = 2;
      }

      is_decided = true;
    }


    // ねじる
    if(type == 0){
      motor.moveDirFast(0, 100);
      // motor.moveDir(0, 100);
      motor.setDirAdd(camera.chance_dir, camera.chance_dir_prev, -7.0f , 0);
    }


    // 平行移動
    else if(type == 1){
      motor.moveDirFast(camera.chance_dir, 100);
      motor.setDirAdd(dir.dir, dir.dir_prev, dir.p_gain, dir.d_gain);

      if(abs(camera.chance_dir) < 2 && state_elapsed > 200) sub.kick();
      if(camera.atk.h > 40) sub.kick();
    }


    // 空いてる方に向ける
    else if(type == 2){
      // motor.moveDirFast(camera.chance_dir, 100);
      motor.moveDirFast(-dir.dir, 100);

      // 一気にゴールに向けるとボールを離してしまうため、出力をコントロールする
      float p_power = state_elapsed / 80;
      if(p_power > 4) p_power = 4;
      motor.setDirAdd(camera.chance_dir, camera.chance_dir_prev, -dir.p_gain * p_power, dir.d_gain * 0);

      if(abs(camera.chance_dir) < 2 && state_elapsed > 200) sub.kick();
      if(camera.atk.h > 36) sub.kick();
    }
    else{
      type = 0;
    }


    // 白線処理
    if(line.on) line_flag = 2;


    // ボールを保持していない -> 回り込みなおす
    if(!ball.is_hold) {
      is_decided = false;
      state = State::Follow;
    }

    // ボールなし -> ボールなし
    if(!ball.is_exist) {
      is_decided = false;
      state = State::NoBall;
    }

    if(state_elapsed > 2500 || dir.accel_avr < 0.5){
      state = State::Pushing;
    }

    dribble_end = millis();

  }



  // キーパーをどかす
  /*
  else if(state == State::AvoidKeeper){
    // ゴール左側に向かいながら右を狙う
    static bool is_decided = false;
    static float atk_dir = 0;

    if(!is_decided){
      if(camera.atk.dir < 0)  atk_dir = 30;
      else                    atk_dir = -30;
    }


    motor.moveDir(-dir.dir, 100);
    motor.setDirAdd(dir.dir-atk_dir, dir.dir_prev, dir.p_gain, dir.d_gain);


    if(!ball.is_hold){
      state = State::Follow;
    }


    // ゴールを中心に捉えた -> シュート
    if(camera.atk.x1-140 < 0 && 0 < camera.atk.x2-140){
      sub.kick();
      state = State::Follow;
    }

    // キーパーがどいた -> ドリブル
  }
  */



  // 押し合い
  else if(state == State::Pushing){
    // 左に押した後、右に切り返す
    if(state_elapsed < 2000){
      if(dir.dir < 0){
        motor.moveDir(push_move, 100);
        motor.setDirAdd(dir.dir+push_dir, dir.dir_prev, dir.p_gain, dir.d_gain);
      }else{
        motor.moveDir(push_move, 100);
        motor.setDirAdd(dir.dir-push_dir, dir.dir_prev, dir.p_gain, dir.d_gain);
      }

    }else{
      motor.moveDir(0, 50);
      if(dir.dir < 0){
        motor.setDirAdd(dir.dir+90, dir.dir_prev, dir.p_gain*4, dir.d_gain);
      }else{
        motor.setDirAdd(dir.dir-90, dir.dir_prev, dir.p_gain*4, dir.d_gain);
      }
    }

    if(line.on) line_flag = 2;



    // 4秒経過 -> ドリブルに戻る
    if(state_elapsed > 3000 || abs(dir.dir) > 50){
      state = State::Dribble;
    }

    // ボールを奪えた -> シュート
    // if(!ball.is_hold){
    //   state = State::Follow;
    // }
  }



  // ok: ボールが取り上げられた
  else if(state == State::NoBall){
    // 真ん中くらいまで下がる
    // if(state_elapsed < 1000){
    //   if(line.on) line_flag = 1;
    //   motor.moveDir(180 - dir.dir, speed_normal*10.0);
    //   motor.setDirAdd(dir.dir, dir.dir_prev, dir.p_gain, dir.d_gain);
    // }else{
    //   if(line.on) line_flag = 1;
    //   motor.moveDir(0, 0);
    // }

    ui.buzzer(440.0f);
    motor.moveDir(0, 0);
    // motor.setDir(dir.dir, dir.dir_prev, dir.p_gain, dir.d_gain);


    // 後ろに見えた -> 逆の回り込み

    // 前に見えた -> 回り込み
    if(ball.is_exist){
      // timer_begin = false;
      state = State::Follow;
    }
  }



  /*
  // ボールを持って後ろに下がる
  else if(state == State::Back){
    // PD
    if(abs(ball.dir)<h){
      move_dir = follow_dir * p_gain - d_gain*(follow_dir -     follow_dir_prev);
      // move_dir = follow_dir;
      h = 45;
    }
    // 円周上
    else if(ball.distance < r){
      float theta = 90 + (r-ball.distance) * 90 / r;
      move_dir = ball.dir + (ball.dir>0?theta:-theta);
      h = 20;
    }
    //接線
    else{
      float theta = degrees(atan2(r, ball.distance));
      move_dir = ball.dir + (ball.dir>0?theta:-theta);
      h = 20;
    }

    // 半分超えたら回り込み直し
    if(camera.atk.h > 24){
      state = State::Follow;
    }
  }
  */



  // ok: 押し込み
  else if(state == State::Oshikomi){
    static bool go_flag = true;
    static int  count = 0;
    static uint32_t timer = millis();

    line_flag = 0;

    // 飛び出さないよう、0.5秒間止める
    if(state_elapsed < 500){
      motor.moveDir(0,0);
    }

    // 進む
    else if(go_flag){
      float move_dir = ball.dir;
      if(ball.dir > 10){
        move_dir = 10;
      }else if(ball.dir < -10){
        move_dir = -10;
      }
      motor.moveDir(move_dir, 50);
      motor.setDirAdd(dir.dir, dir.dir_prev, dir.p_gain*2, dir.d_gain);

      if(ball.is_hold) sub.kick();

      // ギリギリなら戻る
      if(abs(line.dir) > 90 && line.distance > 1.4 || millis() - timer > 1000){
        go_flag = false;
        timer = millis();
      }
    }

    // 下がる
    else{
      motor.moveDir(180, 60);
      motor.setDirAdd(dir.dir, dir.dir_prev, dir.p_gain*2, dir.d_gain);

      if((!line.on && abs(line.dir) < 90) || millis() - timer > 1000){
        go_flag = true;
        count++;
        timer = millis();
      }
    }


    if(count >= 3 || (!line.on && abs(line.dir) < 20 && abs(ball.dir) > 45)){
      count = 0;
      state = State::Follow;
    }

    if(!ball.is_exist){
      state = State::NoBall;
    }

  }


  else if(state == State::Ritsumori){
    if(!camera.atk.is_visible && !camera.def.is_visible){
      motor.moveDir(0, 90);
      motor.setDirAdd(dir.dir, dir.dir_prev, dir.p_gain, dir.d_gain);
    }else if(camera.def.h >= 20){
      if(ball.dir < 0){
        motor.moveDir(-45, 90);
        motor.setDirAdd(dir.dir, dir.dir_prev, dir.p_gain, dir.d_gain);
      }else{
        motor.moveDir(45, 90);
        motor.setDirAdd(dir.dir, dir.dir_prev, dir.p_gain, dir.d_gain);
      }
    }else{
      if(ball.dir < 0){
        motor.moveDir(-90, 90);
        motor.setDirAdd(dir.dir, dir.dir_prev, dir.p_gain, dir.d_gain);
      }else{
        motor.moveDir(90, 90);
        motor.setDirAdd(dir.dir, dir.dir_prev, dir.p_gain, dir.d_gain);
      }
    }

    if(line.on) line_flag = 1;


    if(state_elapsed > 4000 || ball.distance < 12500){
      state = State::Follow;
    }
  }


  // テスト
  else if(state == State::Test){

  }
  else{
    state = State::Follow;
  }



  // 白線処理
  static uint32_t timer = 0;
  static float    back_dir = 0;

  // 速い場合に0.5秒間戻る
  if(millis()-timer < 500){
    motor.moveDirFast(back_dir, 100);
  }
  // 普通
  else{
    switch(line_flag){
    case 1:{

      // ドリブル直後の場合
      if(millis()-dribble_end < 400){
        back_dir = line.dir + 180.0f;
        timer = millis();
      }


      // 反対側のポケットにアクセス
      // 正面を向いている場合
      if(!camera.atk.is_visible && abs(dir.dir) < 15 && abs(line.dir) < 10 && ball.distance > 14000){
        back_dir = 180;
        timer = millis();
      }
      // ゴールの方を向いている場合
      if(abs(line.dir) < 90 && ball.distance > 13000){
        if( (dir_type == 1 && -135 < ball.dir && ball.dir < 45)  ||  (dir_type == 2 && -45 < ball.dir && ball.dir < 135) ){
          back_dir = 180 - dir.dir;
          timer = millis();
        }
      }
      // 自陣コート側
      if(/*!camera.atk.is_visible && */abs(dir.dir) < 15 && abs(line.dir) > 125 && ball.distance > 14000){
        // back_dir = 0;
        // timer = millis();
        state = State::Ritsumori;
      }


      float avoid_dir = 0;

      // 後ろ
      if(line.dir > 157.5 || line.dir < -157.5){
        // if(abs(ball.dir) < 5) avoid_dir = 0;
        /*else*/ if(ball.dir < 0) avoid_dir = -45;
        else                  avoid_dir = 45;
      }
      // 左後ろ
      else if(line.dir < -112.5){
        // if(-135 < ball.dir && ball.dir < 45)  avoid_dir = 0;
        // else                                  avoid_dir = 90;
        if(-90 < ball.dir && ball.dir < 0)      avoid_dir = 0;
        else if(0 < ball.dir && ball.dir < 90)  avoid_dir = 45;
        else                                    avoid_dir = 135;
      }
      // 左
      else if(line.dir < -67.5){
        if(-90 < ball.dir && ball.dir < 90)   avoid_dir = 45;
        else                                  avoid_dir = 135;
      }
      // 左前
      else if(line.dir < -22.5){
        if(-45 < ball.dir && ball.dir < 135)  avoid_dir = 90;
        else                                  avoid_dir = 180;
      }
      // 正面
      else if(line.dir < 22.5){
        // if(abs(ball.dir) < 5) avoid_dir = 180;
        if(ball.dir < 0) avoid_dir = 135;
        else                  avoid_dir = -135;
      }
      // 右前
      else if(line.dir < 67.5){
        if(-135 < ball.dir && ball.dir < 45)  avoid_dir = -90;
        else                                  avoid_dir = -180;
      }
      // 右
      else if(line.dir < 112.5){
        if(-90 < ball.dir && ball.dir < 90) avoid_dir = -45;
        else                                avoid_dir = -135;
      }
      // 右後ろ
      else{
        // if(-45 < ball.dir && ball.dir < 135)  avoid_dir = 0;
        // else                                  avoid_dir = -90;
        if(-90 < ball.dir && ball.dir < 0)      avoid_dir = -45;
        else if(0 < ball.dir && ball.dir < 90)  avoid_dir = 0;
        else                                    avoid_dir = -135;
      }

      motor.moveDir(avoid_dir, 90);  // Edit
      break;

    }
    case 2:
      back_dir = line.dir + 180.0f;
      timer = millis();
      break;
    }

  }


  motor.avr();
  motor.write();
}

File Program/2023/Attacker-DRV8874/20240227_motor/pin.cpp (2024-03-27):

// Arduino Include
#include <Arduino.h>

// Header Include
#include "pin.h"

// Constant
const unsigned short int linePin[22] = { 26, 27, 28, 29, 42, 43, 44, 45, 46, 47, 36, 37, 38, 39, 40, 41, 30, 31, 32, 33, 34, 35 };
const unsigned short int ballPin[16] = { A0, A1, A2, A3, A4, A5, A6, A7, A8, A9, A10, A11, A12, A13, A14, A15 };
const unsigned short int motorPin[4][2] = { { 19, 3 }, { 17, 2 }, { 25, 5 }, { 23, 4 } };
const unsigned short int ledPin[3] = { 13, 14, 15 };
const unsigned short int btnPin[4] = { 7, 8, 9, 10 };
const unsigned short int bzPin = 6;

// Function
// PinMode Setup
void pinSetup() {
  for (int i = 0; i < 22; i++) {
    pinMode(linePin[i], INPUT);
  }
  for (int i = 0; i < 16; i++) {
    pinMode(ballPin[i], INPUT);
  }
  for (int i = 0; i < 4; i++) {
    for (int j = 0; j < 2; j++) {
      pinMode(motorPin[i][j], OUTPUT);
    }
  }
  for (int i = 0; i < 3; i++) {
    pinMode(ledPin[i], OUTPUT);
  }
  for (int i = 0; i < 4; i++) {
    pinMode(btnPin[i], INPUT);
  }
  pinMode(bzPin, OUTPUT);

  Serial.begin(115200);
  return;
}

void waitBtn(int btn) {
  while (true) {
    if (digitalRead(btnPin[btn]) == 1) {
      while (true) {
        if (digitalRead(btnPin[btn]) == 0) {
          break;
        }
      }
      break;
    }
  }

  return;
}

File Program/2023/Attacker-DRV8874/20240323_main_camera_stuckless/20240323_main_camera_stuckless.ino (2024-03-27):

#include "pin.h"
#include "motor.h"
#include "sensor.h"
#include "tone.h"

#include "camera.h"

// Constants
#define DIR_TOLERANCE 10
#define P_GAIN_DIR 0.95
#define D_GAIN_DIR 0.7

#define BALL_MIN 100
#define BALL_FAR 2500
#define MPB_GAIN 0.80

#define LINEF_COUNT 3
#define LINEL_COUNT 2
#define LINEB_COUNT 3
#define LINER_COUNT 2

#define FRONTTURN_TOLERANCE 5000
#define FRONTTURN_TIME 50

#define LEFT_LIM 110
#define RIGHT_LIM 210

PixyI2C pixy(0x54);

// Variables
float dirPrevious = 0;
float diffDiff = 0;

int mpD = 80;
int mpL = 100;
int mpB = 90;

short int justBefore = 0;
short int lineF = 0;
short int lineL = 0;
short int lineB = 0;
short int lineR = 0;

unsigned long frontStart;
bool frontFlag = false;

short int lastGoal = 0;

float mpDir;
float mpLine;
float mpBall;

void setup() {
  pinSetup();
  dirSetup();
  cameraSetup(pixy, 100);
  motorSetup(10, 100, 100, 90, 90);

  while (true) {
    refreshDirRaw();

    if(dir >= 9000){
      tone(bzPin, 440);
      digitalWrite(ledPin[2], 1);
    }
    else{
      noTone(bzPin);
      digitalWrite(ledPin[2], 0);
      if(digitalRead(btnPin[0]) == 1){
        dirOpponent = dir;
        dirCalibration = true;
        waitBtn(0);
        break;
      }
    }

    if(digitalRead(btnPin[0]) == 1 && digitalRead(btnPin[1]) == 1){
      dirCalibration = true;
      refreshDirRaw();
      dirOpponent = dir;
      waitBtn(0);
      noTone(bzPin);
      break;
    }
  }
}

void loop() {
  // check motor lever
  if(digitalRead(btnPin[3]) == 1){
    motorP(0, 0, 0, 0, 100);
    return;
  }

  // dir
  refreshDir();

  if((-1*DIR_TOLERANCE < dir && dir < DIR_TOLERANCE) == false){
    digitalWrite(ledPin[0], 1);
    mpDir = (dir * P_GAIN_DIR + diffDiff * D_GAIN_DIR) * (-1);
    motorRaw(mpDir, mpDir, mpDir, mpDir, mpD);
    diffDiff = abs(dir) - abs(dirPrevious);
    dirPrevious = dir;
    return;
  }

  digitalWrite(ledPin[0], 0);

  // line
  refreshLine();
  
  if(lineBlock[4] != 0){
    digitalWrite(ledPin[1], 1);
    frontStart = millis();
    
    switch(lineBlock[4]){
    case 1111:
      motorP(0, 0, 0, 0, mpL);
      break;

    case 101:
      if(justBefore == 1 || justBefore == 2 || justBefore == 3){
        motorP(100, -100, -100, 100, mpL);
        break;
      }
      else if(justBefore == 5 || justBefore == 6 || justBefore == 7){
        motorP(-100, 100, 100, -100, mpL);
        break;
      }
      else{
        motorP(0, 0, 0, 0, mpL);
        break;
      }

    case 1010:
      if(justBefore == 0 || justBefore == 1 || justBefore == 7){
        motorP(-100, -100, 100, 100, mpL);
        break;
      }
      else if(justBefore == 4 || justBefore == 3 || justBefore == 5){
        motorP(100, 100, -100, -100, mpL);
        break;
      }
      else{
        motorP(0, 0, 0, 0, mpL);
        break;
      }

    case 1000:
    case 1101:
      motorP(-100, -100, 100, 100, mpL);
      if(lineF > LINEF_COUNT && lastGoal == 0){
        motorP(0, 0, 0, 0, mpL);
        delay(250);
        motorP(75, 75, -75, -75, mpB*MPB_GAIN);
        delay(150);
        motorP(0, 0, 0, 0, mpL);
        delay(250);
        motorP(-75, -75, 75, 75, mpB*MPB_GAIN);
        delay(300);
        motorP(0, 0, 0, 0, mpL);
        delay(250);
        lineF = 0;
        lineL = 0;
        lineB = 0;
        lineR = 0;
        justBefore = 4;
        frontStart = millis();
      }
      else if(lineF > LINEF_COUNT){
        delay(150);
        lineF = 0;
        lineL = 0;
        lineB = 0;
        lineR = 0;
        justBefore = 4;
        break;
      }
      justBefore = 4;
      lineF += 1;
      lineL = 0;
      lineB = 0;
      lineR = 0;
      break;

    case 100:
    case 1110:
      motorP(100, -100, -100, 100, mpL);
      if(lineL > LINEL_COUNT){
        delay(150);
        lineF = 0;
        lineL = 0;
        lineB = 0;
        lineR = 0;
        justBefore = 6;
        break;
      }
      justBefore = 6;
      lineF = 0;
      lineL += 1;
      lineB = 0;
      lineR = 0;
      break;

    case 10:
    case 111:
      motorP(100, 100, -100, -100, mpL);
      if(lineB > LINEB_COUNT){
        delay(150);
        lineF = 0;
        lineL = 0;
        lineB = 0;
        lineR = 0;
        justBefore = 0;
        break;
      }
      justBefore = 0;
      lineF = 0;
      lineL = 0;
      lineB += 1;
      lineR = 0;
      break;

    case 1:
    case 1011:
      motorP(-100, 100, 100, -100, mpL);
      if(lineR > LINER_COUNT){
        delay(150);
        lineF = 0;
        lineL = 0;
        lineB = 0;
        lineR = 0;
        justBefore = 2;
        break;
      }
      justBefore = 2;
      lineF = 0;
      lineL = 0;
      lineB = 0;
      lineR += 1;
      break;

    case 1100:
      motorP(0, -100, 0, 100, mpL);
      delay(100);
      justBefore = 5;
      break;

    case 110:
      motorP(100, 0, -100, 0, mpL);
      delay(100);
      justBefore = 7;
      break;

    case 11:
      motorP(0, 100, 0, -100, mpL);
      delay(100);
      justBefore = 1;
      break;

    case 1001:
      motorP(-100, 0, 100, 0, mpL);
      delay(100);
      justBefore = 3;
      break;
    }
    return;
  }

  digitalWrite(ledPin[1], 0);
  
  // ball
  refreshBall();

  if(ballSum < BALL_MIN){
    motorP(0, 0, 0, 0, 100);
    digitalWrite(ledPin[2], 0);
    frontStart = millis();
    frontFlag = false;
    return;
  }

  digitalWrite(ledPin[2], 1);
  if(ballSum < BALL_FAR){
    // ボールは遠い
    tone(bzPin, soundPitch[11]);
    switch(ballBig){
    case 0:
    case 1:
    case 15:
      motorP(100, 100, -100, -100, mpB);
      justBefore = 0;
      frontStart = millis();
      frontFlag = false;
      break;

    case 2:
      motorP(0, 100, 0, -100, mpB);
      justBefore = 1;
      frontStart = millis();
      frontFlag = false;
      break;

    case 3:
    case 4:
      motorP(-100, 100, 100, -100, mpB);
      justBefore = 2;
      frontStart = millis();
      frontFlag = false;
      break;

    case 5:
    case 6:
      motorP(-100, 0, 100, 0, mpB);
      justBefore = 3;
      frontStart = millis();
      frontFlag = false;
      break;

    case 7:
    case 9:
      motorP(-100, -100, 100, 100, mpB);
      justBefore = 4;
      frontStart = millis();
      frontFlag = false;
      break;

    case 8:
      motorP(0, -100, 0, 100, mpB);
      justBefore = 5;
      frontStart = millis();
      frontFlag = false;
      break;

    case 10:
    case 11:
      motorP(0, -100, 0, 100, mpB);
      justBefore = 5;
      frontStart = millis();
      frontFlag = false;
      break;

    case 12:
    case 13:
      motorP(100, -100, -100, 100, mpB);
      justBefore = 6;
      frontStart = millis();
      frontFlag = false;
      break;
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

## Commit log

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2024-04-10 メイン基板・MD基盤の更新
    メイン基板 : ネオピクセルをPWM出力可能なピンに設定
    MD基盤 : 電源回路の作成 DRV887x系の回路図参考・DRV8874製品ページ画像参考の2通りの回路を作成
    [MD-20240410.kicad_sch, Main-20240325.kicad_sch]
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2024-04-11 メイン基板を再度更新
    回路図を開けないエラーを修正しました
    [Main-20240325.kicad_sch]
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2024-04-11 メイン基板・MD基板の回路図を更新しました
    10ピンコネクタの追加 電源電圧の修正
    [MD-20240410.kicad_sch, Main-20240325.kicad_sch]
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2024-04-11 メイン基板・MD基板を修正しました
    DR 2024.04.11 を参考に、メイン基板・MD基板を修正しました
    [MD-20240410.kicad_sch, Main-20240325.kicad_sch]
2024-04-11 キッカーの回路図を修正しました
    DR 2024.04.11を参考にキッカー基板を修正しました
    [Kicker-20240411.kicad_sch]
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2024-04-12 キッカー基板のPCBを更新
    基板裏面のベタVCCの範囲及び、細くなっている部分の修正
    [Kicker-20240411.kicad_pcb]
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2024-04-13 キッカー基板のPCBを修正
    シルクスクリーンの修正
    [Kicker-20240411.kicad_pcb]
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2024-04-14 Auto stash before merge of "main" and "origin/main"
    [Kicker-20240411.kicad_pcb]
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2024-04-15 MD・ラインセンサの回路図を更新
    メイン→ラインセンサ→MD と配線していたのを、
    メイン→MD→ラインセンサ と経由するように変更した。
    ラインセンサの回路図へ、コンパレータを使用するパターンの回路を追加で作成した。
    [Line-20240325.kicad_sch, MD-20240410.kicad_pcb, MD-20240410.kicad_sch]
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2024-04-16 キッカー・MD・ラインセンサ・電源基板を更新
    キッカー :
    ・基板外形変更後のPCBの修正が途中で止まっていたため、残りの部分を編集した
    ラインセンサ :
    ・以前のラインセンサ回路を、コンパレータを使用する回路へと置換した
    ・ラベル line_threshold を、PWM出力可能な5番ピンに設定した
    MD :
    ・キッカーもMD基板を経由させるように変更した
    ・ラインセンサ用にレベル変換回路を作成した
    電源基板 :
    ・フットプリントを一部指定した
    ・基板外形をインポートした
    [Kicker-20240411.kicad_pcb, Kicker-20240411.kicad_sch, Line-20240325.kicad_sch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]
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2024-04-18 MDのPCBを更新
    ・XT30コネクタへの変更
    ・DRV8874のビア・オン・パッドの修正
    ・ベタの拡張
    [MD-20240410.kicad_pcb, MD-20240410.kicad_sch]
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2024-04-20 MD回路のDR修正版-1
    SLEEPは修正していません
    [MD-20240410.kicad_pcb]
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2024-04-21 電源基板のDR修正
    VINのベタを実線へ変更
    [Power-20240325.kicad_pcb]
2024-04-22 キッカー基盤のPCBを修正
    回路図の変更に伴うPCBの修正
    [Kicker-20240411.kicad_pcb, Kicker-20240411.kicad_sch]
2024-04-22 キッカー基板のPCBを修正
    DR終了後の手直しなど
    [Kicker-20240411.kicad_pcb]
2024-04-23 キッカー基板 修正
    [Kicker-20240411.kicad_pcb, Power-20240325.kicad_pcb]
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2024-04-23 ラインセンサ基板の回路図を修正
    仮完成したのでDRをお願いします。
    [Line-20240325.kicad_sch]
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2024-04-23 ラインセンサ基板の回路図 DR
    明確なミスと思われるものを修正しておきました。
    [Line-20240325.kicad_sch]
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2024-04-24 キッカー基板の回路図 DR
    昇圧回路のツェナーダイオード部分を修正しました。
    [Kicker-20240411.kicad_sch]
2024-04-24 キッカー基板の回路図 DR #2
    マージに失敗したため再アップロードです
    [Kicker-20240411.kicad_sch]
2024-04-24 キッカー基板の回路図 DR #3
    度々すみません。回路図の修正について、一部ミスしていたため再アップロードしました。
    [Kicker-20240411.kicad_sch]
2024-04-25 キッカー基板 回路図 修正
    [Kicker-20240411.kicad_sch]
2024-04-25 キッカー基板 PCB 修正版
    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
    [Kicker-20240411.kicad_pcb, Kicker-20240411.kicad_sch]
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2024-04-25 マージのミスを修正
    [Kicker-20240411.kicad_pcb, Kicker-20240411.kicad_sch]
2024-04-25 キッカー基板のPCBを修正し、JLCPCB用の出力ファイルを追加
    [BOM-Kicker-20240411.csv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]
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2024-04-29 Ui基板の回路図・PCBデザインを更新しました
    DR & 修正・SW-4に関する変更
    [UI-20240325.kicad_pcb, UI-20240325.kicad_sch]
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2024-05-02 ペリフェラルのミスを修正
2024-05-02 ペリフェラルのミスを修正2
2024-05-06 メイン基板の回路図を修正しました
    ESP32C3の使用禁止ピンなどの修正
    [Main-20240325.kicad_sch]
2024-05-06 ESP32C3周りの修正を手直ししました
    [Main-20240325.kicad_sch]
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2024-05-17 メイン基板の回路図を修正しました
    [Main-20240325.kicad_sch]
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2024-05-18 電源基板のPCBを修正し、JLCPCB用出力ファイルを作成
    [#006 power-outline.dxf, BOM-Power-20240325.csv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]
2024-05-18 電源基板のPCBを修正しました
    [Power-20240325.kicad_pcb]
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2024-05-19 ライン・MD基板の回路図を更新しました
    ライン-MD間のコネクタのミスを修正
    [Line-20240325.kicad_sch, MD-20240410.kicad_sch]
2024-05-19 メイン基板の回路図を修正しました
    ・RX・TXの逆転の修正
    ・ESP32C3のpin9への印加電圧を5V→3.3Vへ修正
    [Main-20240325.kicad_sch]
2024-05-19 メイン基板の回路図を修正
    [Main-20240325.kicad_sch]
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2024-05-20 メイン基板の回路図を修正した
    [Main-20240325.kicad_sch]
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2024-05-25 キッカー基板の回路図・PCBを修正した
    特にMD-キッカーあたりの確認をおねがいします
    [Kicker-20240411.kicad_pcb, Kicker-20240411.kicad_sch]
2024-05-25 キッカー基板のシルクスクリーンを修正
    #001 → #002
    [Kicker-20240411.kicad_pcb]
2024-05-25 キッカー基板のPCBに細かい修正をかけた
    テキストなど
    [CPL-Kicker-20240411.csv, Kicker-20240411-CuBottom.gbr, Kicker-20240411-CuTop.gbr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]
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2024-05-26 メイン基板の回路図 PCBを修正した
    [Main-20240325.kicad_pcb, Main-20240325.kicad_sch]
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2024-05-26 メイン基板の回路図 PCBを修正
    TX RXの修正 / ball01 ball02を接続
    [Main-20240325.kicad_pcb, Main-20240325.kicad_sch]
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2024-05-26 メイン基板のPCBを回路図の修正に合わせて更新
    [BOM-Main-20240325.csv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]
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2024-06-09 電源入力のLEDのつけ忘れを慌てて修正
    [002-Bottom-002.stl, 002-Top-002.stl]
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2024-06-25 旧機体のプログラムを更新した
    ・ラインセンサの処理順位を最高にした
    ・前方3つめのラインセンサを無視して前進できるようにした
    ・その他色々修正した
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2024-07-08 ドリブラの回路図を修正した
    ENの1ピン制御に切り替えた
    [Dribbler-20240708.kicad_sch, Line-20240325.kicad_pcb]
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2024-07-12 ラインセンサ基板のフットプリントを指定したりした
    書き込み周りを修正した
    [Line-20240325.kicad_sch]
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2024-07-13 ライン基板のPCBを修正した
    基板端クリアランス以外修正した
    [Line-20240325.kicad_pcb, Line-20240325.kicad_sch]
2024-07-14 ライン基板のPCBを再度修正した
    DRC違反(基板端クリアランス)を一応解決した
    [Line-20240325.kicad_pcb]
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2024-07-16 ライン基板のPCBを修正した
    コネクタを裏面につけた
    [Line-20240325.kicad_pcb]
2024-07-16 MD基板を修正したよ
    XH4ピンの位置を裏側・内側へ直した
    [Line-20240325.kicad_sch, MD-20240410.kicad_pcb, MD-20240410.kicad_sch]
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2024-07-17 MD基板を修正した
    [MD-20240410.kicad_pcb, MD-20240410.step]
2024-07-17 MD基板のPCBを修正し製造用ファイルを出力した
    [BOM-MD-20240410.csv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]
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2024-07-19 BNO055のフットプリントを修正した
    [Main-20240325.kicad_pcb, Main-20240325.kicad_sch]
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2024-07-21 MD基板 修正
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2024-07-24 ラインセンサ基板 配線フィレット ほぼ完成
    あとクリアランス違反解消するだけ
    [Line-20240325.kicad_pcb, Line-20240325.kicad_sch]
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2024-07-26 ラインセンサ基板の回路図を修正した
    [Line-20240325.kicad_sch]
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2024-07-26 フットプリントを修正した
    [Line-20240325.kicad_pcb, Line-20240325.kicad_sch]
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2024-07-29 ライン基板の配線を直した
    IN- に line_threshold を繋ぐように変更した
    [Line-20240325.kicad_pcb, Line-20240325.kicad_sch]
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2024-08-01 MD基板 電源用XTコネクタ フットプリント修正済み
    ごめんなさい
    [CPL-MD-20240410.csv, MD-20240410-CuBottom.gbr, MD-20240410-CuTop.gbr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]
2024-08-01 キッカー基板の修正をした
    製造用ファイルも出力しておいた
    [BOM-Kicker-20240411.csv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]
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2024-08-02 キッカーのミスを修正した
    製造用ファイル出力しなおして～
    [Kicker-20240411.kicad_pcb]
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2024-08-05 白浜用のテストプログラムを更新した
    ・ボールセンサ動作確認
    ・モーター回転方向修正完了
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2024-08-08 姿勢制御周り修正したやつ
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2024-08-08 基板に所々修正をほどこした
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2024-08-08 UI基板を修正/MD基板を修正/メイン基板を作り直し （ver.002）
    [BOM-MD-20240410.csv, BOM-UI-20240325.csv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]
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2024-09-14 ATmega2560の評価基板の回路図修正
    セラロック発振器に変更した、回路図は山本さんに確認取中
    [Line-ATmega2560-20240913.kicad_sch]
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2024-09-18 add: 電源基板保護部品/ハンドルの3Dプリンタ用ファイルを追加
    電源基板はラフトなし、充填率30%がうまくいった（ハニカム構造がいい感じに模様っぽくなった）
    ハンドルはラフトなし、充填率100%で印刷中
    [[iot2][001][handle].stl, [iot2][001][power-cover].stl, [iot2][002][handle].stl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]
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2024-09-18 ライン回路修正
    とりあえずICSPつけた
    [Line-20240325.kicad_sch]
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2024-09-19 add: 3Dプリンタ用ファイルを追加
    ボールセンサカバー ver.004
    ネオピクセルカバー ver.002
    [[iot2][001][ball-cover].stl, [iot2][001][old-ball-cover].stl, [iot2][002][neopixel-cover].stl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]
2024-09-19 add: 3Dプリンタ用ファイルを追加
    ネオピクセル カバー ver.003
    [[iot2][003][neopixel-cover].stl]
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2024-09-19 update: メイン基板を編集した
    サブマイコンまわり
    謎が多い...
    [Main-20240325.kicad_sch]
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2024-09-20 add: オムニホイールのCNC切削用ファイルを追加
    CNCにて切削中
    火曜日に確認の必要アリ
    [[006][iot2][omni][maxon][misumi].dxf]
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2024-09-20 update: カメラ周り修正した
    [Main-20240325.kicad_sch]
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2024-09-21 update: メイン基板の回路図/PCBを編集した
    ESP32周り / ボールセンサ配置
    [Main-20240325.kicad_pcb, Main-20240325.kicad_sch]
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2024-09-23 add: 3Dプリンタ出力用ファイルを追加
    カメラ台とカメラのストッパー
    ミラー台
    [[iot2][001][camera-supporter][main].stl, [iot2][001][camera-supporter][stopper].stl, [iot2][001][mirror-supporter].stl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]
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2024-09-23 update: メイン基板の回路を更新
    カメラ周りとかを直した
    リファクタリングちょっとした
    [Main-20240325.kicad_sch]
2024-09-24 update: コンフリクトの修正
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2024-09-24 add: M5Stack Cam S3のピッチ変換基板を作成した
    回路・PCBともに設計完了した
    [BOM-M5StackCam-20240924.csv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]
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2024-09-25 update:ボールの角度によるズレを修正するやつ
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2024-09-27 update: ラインセンサ基板の回路とPCBを修正した
    電源をVINピンではなく+5Vピンに入れるように変更した
    [Line-20240325.kicad_pcb, Line-20240325.kicad_sch]
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2024-10-11 update: 基板配線を進めた + カメラのテストプログラムを更新した
    [M5StackCam-20240924.kicad_pcb]
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2024-10-16 update: メイン基板のPCBデザインをすすめた
    ボールセンサ用ローパスフィルタのコンデンサ/抵抗の配置が悩ましい
    4層基板でいくってことでいいよね？
    [Main-20240325.kicad_pcb, Main-20240325.kicad_sch]
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2024-10-24 update: ラインセンサ基板ver.002を更新した
    回路図をちょっと進めた ∧ PCBをやり始めた
    [Line-002-20241023.kicad_pcb, Line-002-20241023.kicad_sch]
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2024-10-24 update: ラインセンサ ver.002 の回路図を進めた
    コンパレータを追加
    ピンアサインはちょっと悩み中だけどほぼいい感じだと思う...たぶん。
    [Line-002-20241023.kicad_pcb, Line-002-20241023.kicad_sch]
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2024-10-25 add: update: ラインセンサ基板の外形の更新版を追加 & PCBデザイン/回路図を進めた
    [Line-002-20241023.kicad_pcb, Line-002-20241023.kicad_sch, [iot2][002][line-002-outline].dxf]
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2024-10-26 update: UI基板のグローバルラベル名が間違っていたのを修正した
    [UI-20240325.kicad_sch]
2024-10-26 update: NeoPixel基板のグローバルラベルの向きが間違っていたのを修正
    [NeoPixel-20240808.kicad_sch]
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2024-10-26 update: メイン基板の回路図のDRを進めた & PCBをちょっとやった
    [Main-20240325.kicad_pcb, Main-20240325.kicad_sch]
2024-10-26 update: ラインセンサ基板 ver.002 の回路図とPCBを進めた
    [[iot2][001][line-002-outline].dxf, [iot2][002][line-002-outline].dxf]
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2024-10-27 update: メイン基板の部品の裏表などを修正
    [Main-20240325.kicad_pcb, Main-20240325.kicad_sch]
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2024-11-02 clean: コンフリクトを修正
    [Dribbler-20240708.kicad_sch, Main-20240325.kicad_pcb, Main-20240325.kicad_sch]
2024-11-02 update: #回路・基板 のチャンネルでの議論に沿って回路図を編集した
    @rts DRお願い
    [Main-20240325.kicad_sch]
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2024-11-02 update: コンフリクトを修正した
    [Main-20240325.kicad_sch]
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2024-11-03 update: メイン基板の回路図を修正した
    [Main-20240325.kicad_sch]
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2024-11-07 clean: ファイル名の変更
    プログラムのファイル名が内容と不一致だったのを修正
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2024-11-07 update: メイン基板 ver.002 のPCBデザインを進めた
    ほぼ完成、PCBのDRをお願いしたい
    [Main-20240325.kicad_pcb, Main-20240325.kicad_sch]
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2024-11-10 update: メイン基板のPCBを更新した
    ボタンをSMD→THTに変更
    FPCコネクタを裏面に配置
    発注用ファイルを出力
    [BOM-Main-20240325.csv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]
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2024-11-11 update: ラインセンサの修正
    D7 D11 修正完了
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2024-11-12 update: UI基板のボタンの1つが+3.3Vに接続されていなかったのを修正した
    [UI-20240325-CuBottom.gbr, UI-20240325-CuTop.gbr, UI-20240325-EdgeCuts.gbr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]
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2024-11-14 update: MD基板のNchMOSFET部分の設計を修正した
    ピンアサインも確認したから大丈夫だと思う
    [BOM-MD-20240410.csv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]
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2024-11-16 update: VCCのベタが細くなっていたのを修正した
    [MD-20240410.kicad_pcb]
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2024-12-04 update: ボールの接線方向に対して動くように修正した
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2024-12-10 add: 旧機体用オムニホイールの設計修正版の3Dプリンタ印刷用ファイルを追加した
    [[iot2][004][omni-old][outside].stl]
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2024-12-14 update: メインマイコンのピンを修正した
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2024-12-14 update: FPCケーブルのPCBデザインを修正した
    裏面のベタを削除して各個独立した配線になるようにした
    [FPC-MD-Main-20240719-CuBottom.gbr, FPC-MD-Main-20240719-CuTop.gbr, FPC-MD-Main-20240719-EdgeCuts.gbr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]
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2024-12-15 update: 新機体のピンアサインなどを修正した
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2024-12-16 add: update: fix: remove:
    [[iot2][001][dribbler-003].stl, [iot2][003][dribbler-004][lid].stl, [iot2][003][dribbler-004][main].stl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]
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2024-12-17 update: メイン基板ver.003 を更新した
    キッカー用5ピンも配置した
    DRは一通りやったけどそっちでも1回やってみてほしい
    [Main-20241217.kicad_pcb]
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2024-12-19 add: MD ver.001 のアーカイブを追加した
    [Kicker-20240411.kicad_pcb, Kicker-20240411.kicad_sch, MD outline #001.dxf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]
2024-12-19 add: キッカー ver.002 のアーカイブを追加した
    [kicker outline #004.dxf, kicker outline #005.dxf, kicker outline #006.dxf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]
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2024-12-21 オムニホイールの出力用ファイルを修正した
    [[iot2][006][omni-old][inside].stl, [iot2][006][omni-old][outside].stl]
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2024-12-22 add: ラインセンサ基板 ver.003 を追加した
    今後はこのプロジェクトフォルダをいじっていっていこう
    [Line-003-20241222.kicad_pcb, Line-003-20241222.kicad_sch, [iot2][001][line-003-outline].dxf]
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2024-12-24 add: FPC ver.004 のファイルを追加した
    [BOM-FPC-MD-Main-002-20241115.csv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]
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2024-12-24 update: FPC ver.004 に更新した
    プロジェクトファイル自体は一番初めのモノを使用してるよ
    [BOM-FPC-MD-Main-002-20241115.csv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]
2024-12-24 add: ドリブラー基板 ver.002 のプロジェクトファイルを追加
    [#001.dxf, Dribbler-002-20241225.kicad_pcb, Dribbler-002-20241225.kicad_sch]
2024-12-24 update: ラインセンサ基板 ver.003の回路図を更新した
    使ってないからbuzzerいらない？
    [Line-003-20241222.kicad_sch]
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2024-12-25 update: ラインセンサ基板 ver.003 の回路図を編集・更新した
    [Line-003-20241222.kicad_sch]
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2024-12-25 update: ラインセンサ基板 ver.003 を更新した
    回路図のDRをした
    いろいろ問題点ありそうだから、明日もう一回DRし直してからPCBいこか
    出来れば明日、無理なら明後日ぐらいまでに必ず完成させよう！！
    [Line-003-20241222.kicad_pcb, Line-003-20241222.kicad_sch, [iot2][002][line-003-outline].dxf]
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2024-12-26 add: ラインセンサ基板 ver.003を更新した
    あと3Dプリンタ印刷用ファイルも追加した
    [Line-003-20241222.kicad_pcb, Line-003-20241222.kicad_sch, [iot2][003][line-003-outline].dxf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]
2024-12-26 update: ラインセンサ基板の回路とPCBを更新した
    閾値用PWMの周波数選択用のジャンパの削除
    基板外形の更新
    など
    [Line-003-20241222.kicad_pcb, Line-003-20241222.kicad_sch, [iot2][005][line-003-outline].dxf]
2024-12-26 update: ラインセンサ基板のPCBを更新した
    部品配置はひととおりやったから配線を頼む
    配線難しかったり逆に基板外形が大きすぎたらまた連絡して
    [Line-003-20241222.kicad_pcb]
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2025-01-05 update: アタッカーのピンを修正した
    EN1 ~ PH4 の全部が逆
    [MD_ver003.kicad_pcb, MD_ver003.kicad_sch]
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2025-01-06 update: カメラのバグを修正した
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2025-01-06 update: キッカー基板の回路図を修正した
    ツェナーダイオードをなくした
    +48V-+VDD関連のNchMOSFETのロジックを削除した
    [Kicker-20240411.kicad_pcb, Kicker-20240411.kicad_sch]
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2025-01-08 update: 角度計算のバグを修正した
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2025-01-11 update: 押し込みに遷移するときのバグを修正した
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2025-02-19 update: モーターの回転方向を修正した
2025-02-19 update: ラインセンサのバグを修正した
    キーパーやるまで全く気づかなかった
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2025-02-22 update: キーパーが動かなくなるバグを修正した
    0除算
2025-02-22 update: キーパーを色々修正した
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2025-03-13 saved UNDO information for reset changes and discarded files
    [Teensy4.1.ino]
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
